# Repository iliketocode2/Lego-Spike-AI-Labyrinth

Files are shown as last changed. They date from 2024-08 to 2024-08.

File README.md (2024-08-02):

# Build and Program the AI Spike Labyrinth
<h3>OpenMV & Uart, Q-learning, Bluetooth, and Pyscript (With extra js)</h3>
<p>The goal of this project was to explore potential roles for the Lego Spike Prime in a system with external devices and heavy computation and graphical display. This repository contains all of the necessary code and instructions for you to recreate a similar project should you choose to do so. In addition, if you are looking here for specific Spike-related processes (such as connecting to the Spike with Bluetooth or using Pyscript with the Spike in general) parts of my code feature comments and explanations of these applications.</p>

> [!WARNING]
> Much of the code in this project is custom to my setup (i.e., motor starting values and other constants). However, I have identified these variables in my code, so it is necessary to read files carefeully before executing them. In addition, this project contains many existing bugs. Feel free to create issues for this repository.

## Communication Overview
commnication flow chart
- Solid lines depict physical connection; dotted lines depict ble connection.
- Double-sided arrows indicate two-way communication (send and receive) data, single sided arrows represent one-way communication.

## Website Overview
The [website](https://iliketocode2.github.io/Lego-Spike-AI-Labyrinth/) (what you will have displayed on your screen after running the code in an IDE with HTML preview features) features two primary modes: Free Play mode and AI mode. Within Free Play mode there are two sub modes: (x, y) mapping and (pitch, roll) mapping. 
- To enter Free Play mode, draw labyrinth walls, select a start and end square, and select ‘no’ when the popup prompts you to draw the path. Then, to toggle between (x, y) and (pitch, roll) mode, change the toggle on the bottom of the screen. The (x, y) mode uses coordinates sent from the script running on the OpenMV camera to move the animated ball. The (pitch, roll) mode uses pitch and roll data from the Spike to simulate the location of the ball (basically running a physics simulation).
- To enter AI mode draw labyrinth walls, select a start and end square, and select ‘yes’ when the popup prompts you to draw the path. To have the Spike move the ball from the start square to the end square press 'Run the Spike along the path'. After the run attempt is complete, the grid will reset if the ball has correctly reached the end square. Otherwise, click 'Manual Stop' to reset the run.

If the orientation of your screen compared to the physical device you build is off, simply rotate the on-screen grid by pressing the arrow button on either side of the grid. 

## Materials
  - ### Hardware
    - Lego Spike
    - OpenMV Cam (I used an R2) with a [custom PCB connector on the back](https://www.instructables.com/Backpack-1-OpenMV-Camera/) -- this will connect to the black section of a lego ultrasonic sensor
    - [Lego pieces](https://www.brickowl.com/catalog/lego-spike-prime-set-45678/inventory): This model contains ~480 pieces</li>
    - [A red Lego ball](https://www.brickowl.com/catalog/lego-red-hard-plastic-ball-52mm-22119-23065) (unless you change the OpenMV color detection/blob code)</li>
    - [Instructions](https://drive.google.com/file/d/1RjmZkfVSPhEm0D2quI89XZbNSfkmIFvk/view?usp=sharing) for the model
    - A cord to connect the Spike Prime to your computer (typically usb to micro usb)
  
  - ### Software
    - [OpenMV IDE](https://openmv.io/pages/download)
    - [Visual Studio Code](https://code.visualstudio.com/download) or another IDE to run Pyscript on: [Pyscript.com](https://pyscript.com), [Github Codespace with Pyscript presetup](https://github.com/ntoll/codespaces-project-template-pyscript), etc
    - [BLE_CEEO.py](https://github.com/chrisbuerginrogers/SPIKE_Prime/blob/main/BLE/BLE_CEEO.py#L1) -- Download this file onto the Spike Prime using [Thonny](https://thonny.org). This IDE is very effective at connecting micropython devices.
  
  - ### Firmware
    - [Custom firmware](https://raw.githack.com/tuftsceeo/SPIKE-html/main/index.html) for the Spike Prime
      - To install:
        1. Turn off the Spike Prime and disconnect it from all devices
        2. Hold down the bluetooth button until it strobes blue, green, pink
        3. Plug in the Spike to your computer
        4. Press 'Connect Up' and follow prompts to install the new firmware
    
> [!IMPORTANT]
> This firmware enables UART communication on the Spike Prime Hub. To restore the original firmware, open the official [Spike IDE](https://spike.legoeducation.com/) and click 'update hub'. Also note that while this firmware is generally excellent, there is a slight bug with the motors that causes oscillation on remote disconnect. This should NOT affect this project.

## Further Reading
- [UART](https://www.analog.com/en/resources/analog-dialogue/articles/uart-a-hardware-communication-protocol.html)
- [BLE](https://novelbits.io/bluetooth-low-energy-ble-complete-guide/)
- [Lego Spike Prime Python Library](https://spike.legoeducation.com/prime/help/lls-help-python#lls-help-python-spm)
- [OpenMV docs](https://docs.openmv.io)
- [Q-learning Explanation](https://www.datacamp.com/tutorial/introduction-q-learning-beginner-tutorial)
- [How to setup Github Pages and VS Code with GitHub](https://shimmering-cesium-c35.notion.site/Summer-of-24-0c8bd589e46b4b8b84bc484837b5b102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)

## Build Render and Web Interface
AI Spike Maze Render and Interface

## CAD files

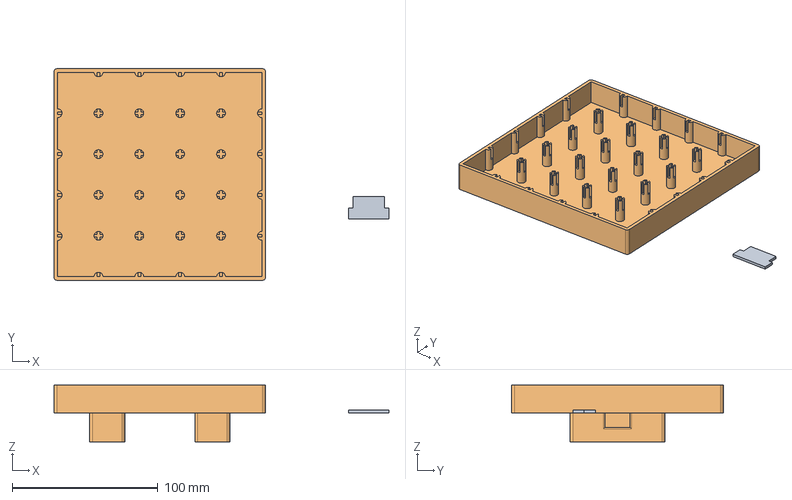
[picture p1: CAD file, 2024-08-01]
AI Spike Maze and Wall.step
229.6 x 145.0 x 39.0 mm

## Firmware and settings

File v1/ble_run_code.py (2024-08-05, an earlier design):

code = f'''
from BLE_CEEO import Yell, Listen
import hub, utime, runloop, sys, time, motor, random
from hub import port, motion_sensor, uart
# import asyncio

#define uart(port, baudrate, timeout)
#port 0-5 = A-F
U = uart.init(2,115200,100)
# Define motor ports (make sure to change these for your setup)
motorY = port.B #geared motor
motorX = port.F
speed = 50

def peripheral(name): 
    # zero motors
    print('Zeroing motors...')
    while (motor.absolute_position(motorX)) != -100:
        motor.run_to_absolute_position(motorX, -100, 100)
    motor.reset_relative_position(motorX)
    while (motor.absolute_position(motorY)) != -125:
        motor.run_to_absolute_position(motorY, -125, 100)
    motor.reset_relative_position(motorY)
    print('Motors zeroed')

    #connect up
    try:
        p = Yell(name, verbose = True)
        if p.connect_up():
            runConnected(p)
    except Exception as e:
        print(e)
    finally:
        p.disconnect()
        print('closing up')
        
def runConnected(me):
    print('ble connected')
    utime.sleep(2)

    while (True):
    
        payload = ''

        if U.any():
            b = U.any()
            message = U.read(b)
            payload += str(message)

        payload += "**"

        payload += str(motion_sensor.tilt_angles())

        payload += "**"

        pos1 = motor.absolute_position(motorX)
        pos2 = motor.absolute_position(motorY)
        payload += "(mX: "
        payload += str(pos1)
        payload += ", mY: "
        payload += str(pos2)
        payload += ")"

        name = 0
        direc = 0

        if me.is_any:
            print('Received incoming')
            incoming = me.read()
            if "!!" in incoming: #if running along path
                print('Running along path')
                parts = incoming.split("!!")
                if len(parts) > 0:
                    p1 = parts[0] 
                    p2 = parts[1]
                    
                AIMotorControl(p1, p2)
                
            else: #if arrow keys pressed
                print('Running using arrow keys')
                parts = incoming.split("**")
                if len(parts) > 0:
                    name = parts[0] 
                    direc = parts[1]

                print('NAME:', name, 'DIREC:', direc)
                manualMotorControl(name, direc)

        me.send(payload)

        if not me.is_connected:
            print('lost connection')
            break
            
        utime.sleep(0.1)               


# def AIMotorControl(x_pos, y_pos):
#     if x_pos == -9000 and y_pos == -9000:
#         wiggle_motors()
#     else:
#         while abs(motor.absolute_position(motorX) - x_pos) > 5 or abs(motor.absolute_position(motorY) - y_pos) > 5:
#             if abs(motor.absolute_position(motorX) - x_pos) <= 5:
#                 motor.stop(motorX)
#             else:
#                 if x_pos > motor.absolute_position(motorX):
#                     motor.run(motorX, speed)
#                 else:
#                     motor.run(motorX, -speed)

#             if abs(motor.absolute_position(motorY) - y_pos) <= 5:
#                 motor.stop(motorY)
#             else:
#                 if y_pos > motor.absolute_position(motorY):
#                     motor.run(motorY, speed)
#                 else:
#                     motor.run(motorY, -speed)

#             time.sleep(0.1)


def AIMotorControl(X, Y):
    max_degrees = 45  # Maximum degrees of rotation allowed

    try: 
        x_pos = int(X)
        y_pos = int(Y)
    except:
        print('INVALID: ', X, Y)

    if x_pos == -9000 and y_pos == -9000:
        wiggle_motors()
    else:
        # Get starting positions
        start_x = motor.absolute_position(motorX)
        start_y = motor.absolute_position(motorY)

        # Calculate direction
        dir_x = 1 if x_pos > start_x else -1
        dir_y = 1 if y_pos > start_y else -1

        # Start both motors
        motor.run(motorX, speed * dir_x)
        motor.run(motorY, speed * dir_y)

        while True:
            current_x = motor.absolute_position(motorX)
            current_y = motor.absolute_position(motorY)

            x_reached = abs(current_x - x_pos) <= 5
            y_reached = abs(current_y - y_pos) <= 5

            x_exceeded = abs(current_x - start_x) > max_degrees
            y_exceeded = abs(current_y - start_y) > max_degrees

            if x_reached or x_exceeded:
                motor.stop(motorX)
            if y_reached or y_exceeded:
                motor.stop(motorY)

            if (x_reached or x_exceeded) and (y_reached or y_exceeded):
                break

        # Ensure both motors are stopped
        motor.stop(motorX)
        motor.stop(motorY)

        # Return status
        return (x_reached and not x_exceeded) and (y_reached and not y_exceeded)


def wiggle_motors(amplitude=35, duration=4):
    start_x = motor.absolute_position(motorX)
    start_y = motor.absolute_position(motorY)
    
    start_time = time.time()
    while time.time() - start_time < duration:
        dx = random.uniform(-amplitude, amplitude)
        dy = random.uniform(-amplitude, amplitude)
        
        motor.run_to_relative_position(motorX, int(dx), speed)
        motor.run_to_relative_position(motorY, int(dy), speed)
    
    
    # Return to starting position
    motor.run_to_absolute_position(motorX, start_x, speed)
    motor.run_to_absolute_position(motorY, start_y, speed)
    time.sleep(0.2)
        
def manualMotorControl(a, b):
    speed = 100

    leftBound = -140
    rightBound = -35

    leftBound2 = -140
    rightBound2 = -110

    if a == '2': #if no arrow keys pressed stop in place
        motor.stop(motorX)
        motor.stop(motorY)
        
    elif a == '1': #up down
        if motor.absolute_position(motorY) < leftBound2:
            motor.run_to_absolute_position(motorY, leftBound2 + 1, 0 - speed)
        elif motor.absolute_position(motorY) > rightBound2:
            motor.run_to_absolute_position(motorY, rightBound2 - 1, speed)
        else:
            if b == '1':
                motor.run(motorY, 0 - speed)
            elif b == '-1':
                motor.run(motorY, speed)

    elif a == '0': #right left
        if motor.absolute_position(motorX) < leftBound:
            motor.run_to_absolute_position(motorX, leftBound + 1, speed)
        elif motor.absolute_position(motorX) > rightBound:
            motor.run_to_absolute_position(motorX, rightBound - 1, 0 - speed)
        else:
            if b == '1':
                if motor.absolute_position(motorX) < rightBound:
                    motor.run(motorX, 0 - speed)
            elif b == '-1':
                if motor.absolute_position(motorX) > leftBound:
                    motor.run(motorX, speed)

    else:
        print('invalid input')

peripheral('Spike')
'''

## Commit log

2024-07-22 uart integration
    -uart integration to connect openMV cam to spike
    -now receiving xy data from openMV cam detecting red ball pos
2024-07-22 toggle to switch between physics sim and ai x, y coords
2024-07-29 PID update 1
2024-07-29 new motor control for manual mode
2024-07-30 physics running (broken still), updated motor code
    [ble_run_code.py]
2024-07-30 Manual Stop, button changes, ypr fixes
    [ble_run_code.py]
2024-07-30 pre coordinate fixes for path running
    [ble_run_code.py]
2024-07-31 GEARED MOTORS, PID fixes
    [ble_run_code.py]
2024-08-01 3D Printable Model
    [AI Spike Maze and Wall.step]
